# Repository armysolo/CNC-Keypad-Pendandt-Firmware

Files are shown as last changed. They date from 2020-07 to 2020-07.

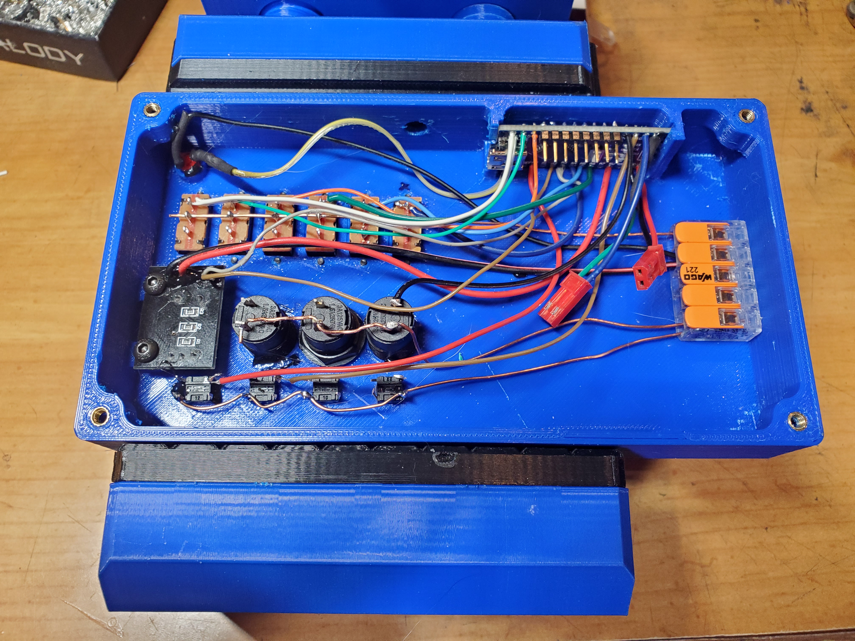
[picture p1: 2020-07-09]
Images/Assembly2.jpg

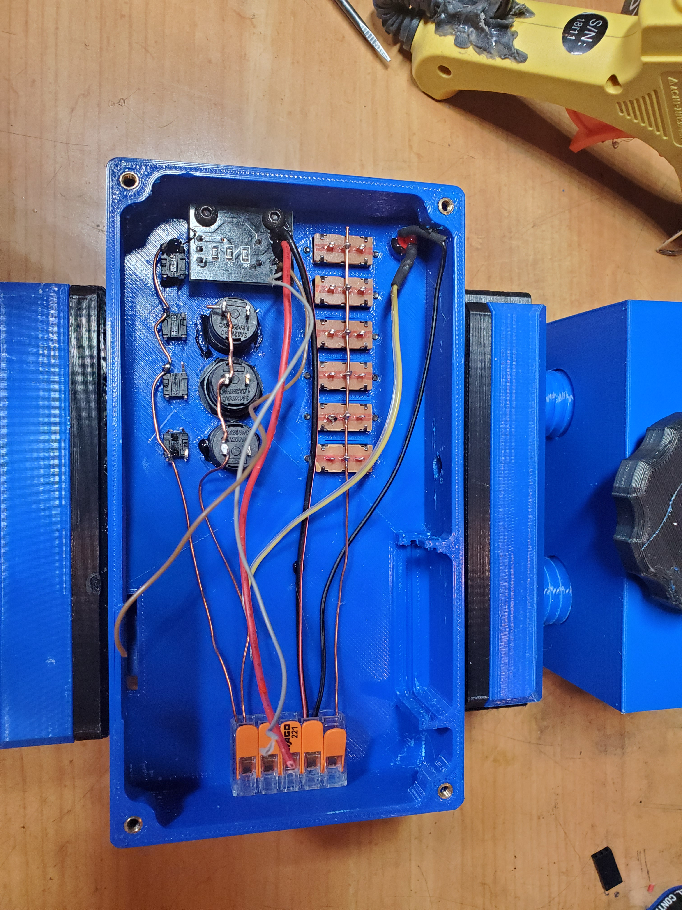
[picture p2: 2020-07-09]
Images/Assembly1.jpg

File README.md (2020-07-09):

# CNC-Pendant-Firmware

Modified CNC Pendant Firmware with Arduino Nano Clone with CH340G microchip. I didn't want to spend $80(USD) on a pendant that limited the functionality to only jogging moves. My branch keeps the functionality of jogging using a rotary encoder and common micro SPDT 1P2T switches but also incorporates a 16 button keypad where you can assign custom G/M codes or even macros. This also maintains Panel Due functionality by passing TX from the Arduino to the Duet board and RX from the Arudino to the Panel Due.

*NOTE: This should work with other Arduino boards like the Arduino Micro Pro. However my testing was done only with a Nano clone so all wiring and sketch notes are based on the Nano. There's residual info/configs from the original fork I didn't want to get rid of.

The Arduino Nano I use come un-soldered. The printed parts I designed are based off Arduino Nano clones without the pins. The parts could still work if modified but for now you'd probably have some fitment issues. You will need to solder pins to D2-D9 for the keypad. Make sure to flip the pins so the longer end of the pins are on the top instead of the bottom.

```
Nano     Connected to:   
VCC      PanelDue side port 5V
GND      PanelDue side port 0V
GND      LED - Terminal, Rotary Encoder Ground, Mini Switch Middle Terminal, Emergency Stop
5v       Rotary Encoder + Terminal, LED + Terminal-Make sure you use the correct resistor to reduce the votage from the Arduino. 120-220 ohm should be sufficient.
A0       Emergency Stop
A1       NC
A2       Rotary Encoder Pin A
A3       Rotary Encoder Pin B
A4       X Switch Top Lug
A5       Y Switch Top Lug
A6       Z Switch Top Lug
A7       NC
D2       Keypad Membrane
D3       Keypad Membrane
D4       Keypad Membrane
D5       Keypad Membrane
D6       Keypad Membrane
D7       Keypad Membrane
D8       Keypad Membrane
D9       Keypad Membrane
D10      X.1 Switch Top Lug
D11      X1 Switch Top Lug
D12      X10 Switch Top Lug
D13      NC
TX1      Through 6K8 resistor to Duet URXD0
RX0      Paneldue Dout Side Port
```

To use the jog features you will need to select your axis and the movement increments by sliding the switch up. So if you slide the X switch up and the x1 switch up, turning the rotary encoder will move the axis in 1mm increments.

Code Explanation
The G/M code you wish to assign to the keypad buttons must have a specific format. The desired G/M code goes in the quotations with "\n" at the end of each code. 

For instance 

    1. this code is assigned to button number 1 and when pressed it sends G28 to the printer. 
      if (key == '1') { output.print("G28\n"); } // Home all

You can assign a button to run multiple G/M codes at once. 

For instance 

    2. this code is assigned to button number 4. When pressed it enables the hotend and sets it's temp to 200. Notice each code must have "\n" after the end of it.
      else if (key == '4') { output.print("T0 P0\n G10 P0 S200\n"); }  // Enable hotend and set temp to 200c

This code is assigned to button number 3.

    3. When pressed it sends; M120-pushes state of the machine to a stack, M83-Sets extruder to relative position, G1-Linear move, E10 F900-Extrude 10mm of filament at 900mm per minute, M121-Recovers last state from stack
      else if (key == '3') { output.print("M120\n M83\n G1\n E10\n F900\n M121\n"); } //Extrude 10mm of filament at 15mm/s

The original sketch included a LED that would illuminate when the Estop was pressed but I found it inconsistent. The LED would often stay lit after the Estop was pressed so my sketch has the LED part removed.

I used the core from door bell wire and daisy chained all the switch grounds to clean up the wiring. 

I installed a latching push button switch where one terminal goes to ground on the Arduino and the other terminal goes to ground for all switches, rotary encoder and LED. Wiring it this way allows me to disable the rotary encoder, tactile switches and slide switches preventing any unwanted movement. When the switch is latched it enables the rotary encoder and all other switches, the LED will light up to let you know everything is grounded/enabled.

**Parts list** These are the links for reference of the parts I puchased:

**Arduino Nano Clone** These boards are so inexepensive and have so many uses I buy them 10 at a time un-soldered. With them unsoldered it's also easier to desolder the resistor on the front leading to the LED and desolder the 1k resistor on the rear and replace it with a 10k resistor. I used a little hot glue from a hot glue gun to secure the resistor to the back of the board to protect it.

**10 Pack un-soldered**
https://www.amazon.com/Longruner-ATmega328P-Controller-Module-Arduino/dp/B01MSYWE6B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

**3 Pack un-soldered**
https://www.amazon.com/WYPH-ATmega328P-Microcontroller-Development-Not-soldered/dp/B07KCH534K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

**2 Position Mini switch** If it's a 3 prong switch the middle lug is the common lug. When the switch is in the bottom position, the circuit for the bottom lug and middle lug are closed while the top lug is open. When the switch is in the top position, the circuit for the top lug and middle lug are closed while the bottom lug is open.
https://www.amazon.com/uxcell-Position-Switch-Solder-SS12F1-G3/dp/B007QAJMHO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

**Keypad membrane** 4x4 16 key keypad membrane
https://www.amazon.com/WINGONEER-Universial-Switch-Keyboard-Arduino/dp/B06XHFC19G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

**KY-040 Rotary Encoder** I desoldered the pins and soldered the wires directly to the board. The push button terminal(SW) is not connected to the Arudino.
https://www.amazon.com/Cylewet-Encoder-15%C3%9716-5-Arduino-CYT1062/dp/B06XQTHDRR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

**6 x 6mm Momentary Tactile Push Button Switch Micro NO/NC** These are 4 pin momentary push button switches. Depending which lugs you solder, the switch can be used as NO(switch circuit is open until pressed) OR NC(switch is closed until pressed). Currently used for Emergency Stop/Reset Button. Can also be used for to assign additional G/M codes.
https://www.amazon.com/gp/product/B071KX71SV/ref=ppx_yo_dt_b_search_asin_title?ie=UTF8&psc=1
**Note: Coding to support additional push button switches in prgoress.

**5mm LEDs**
https://www.amazon.com/MCIGICM-Circuit-Assorted-Science-Experiment/dp/B07PG84V17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

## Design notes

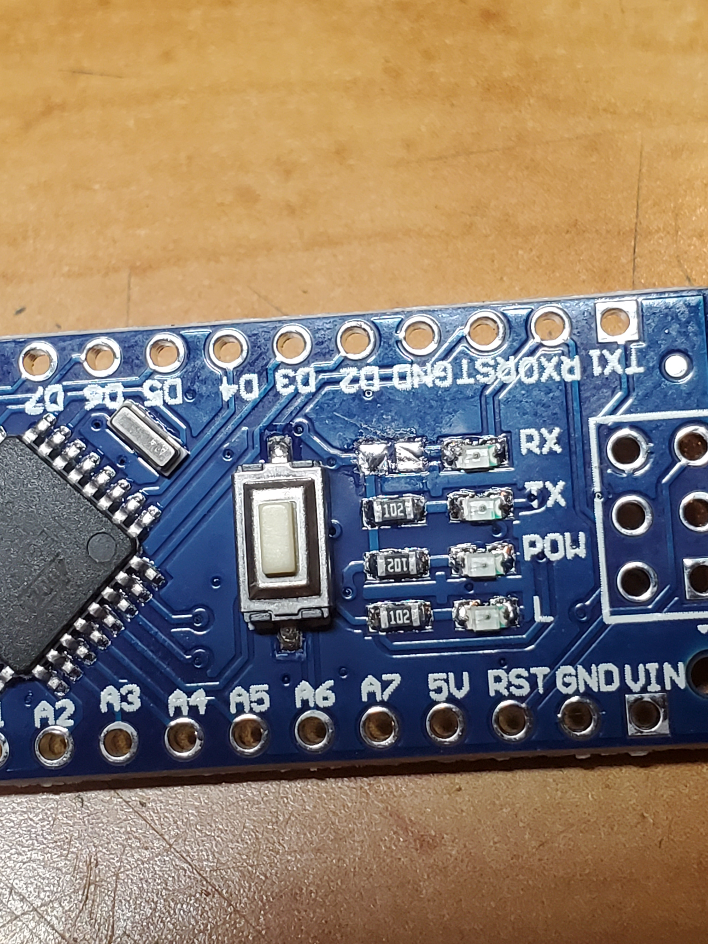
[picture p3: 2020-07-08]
Images/Nano1-2.jpg

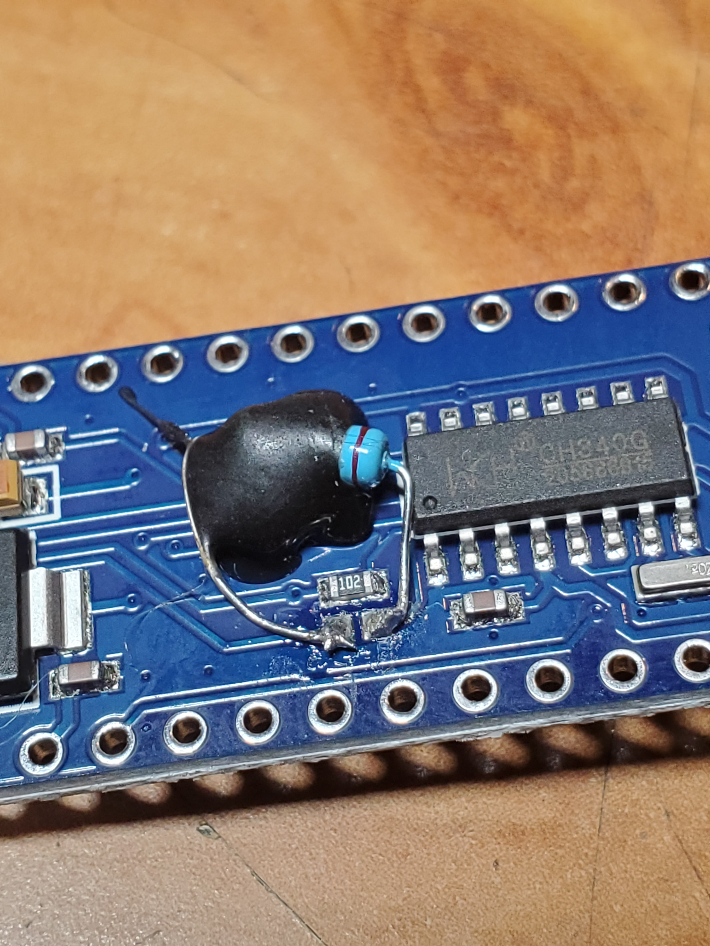
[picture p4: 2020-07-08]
Images/Nano2-2.jpg

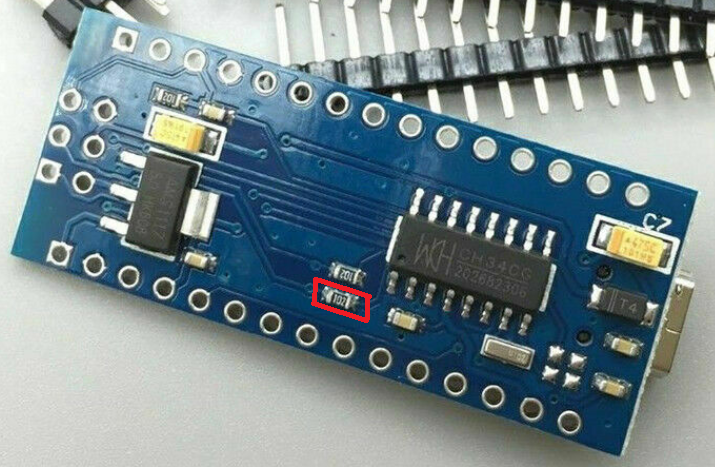
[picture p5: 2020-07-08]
Images/Nano2-1.png

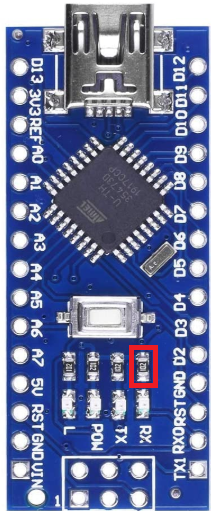
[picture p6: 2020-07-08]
Images/Nano1-1.png

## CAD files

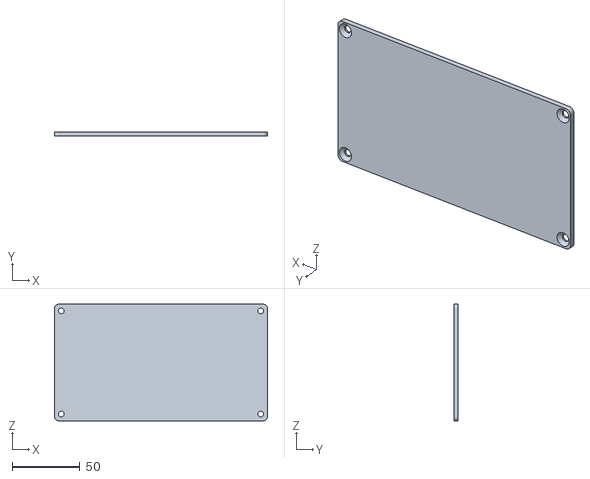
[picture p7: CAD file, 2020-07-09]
Printed Files/Mini Button Back With G Code Sender.STL
157.0 x 3.00 x 86.0

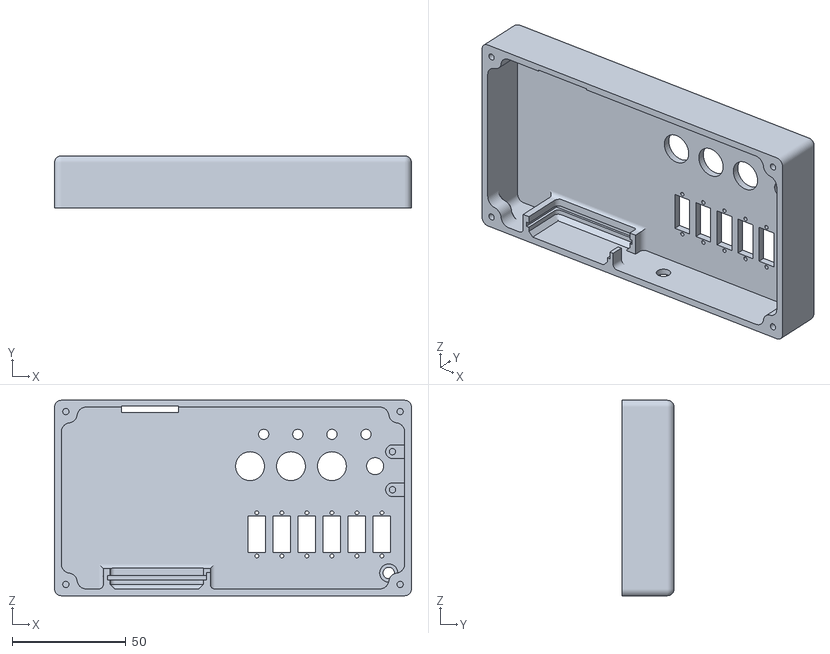
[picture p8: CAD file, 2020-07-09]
Printed Files/Mini Button Mount With G Code Sender.STL
157.0 x 23.0 x 86.0

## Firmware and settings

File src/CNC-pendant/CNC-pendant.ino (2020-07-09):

// CNC pendant interface to Duet
// D Crocker, started 2020-05-04

/* This Arduino sketch can be run on either Arduino Nano or Arduino Pro Micro. 
 * It should alo work on an Arduino Uno (using the same wiring scheme as for the Nano) or Arduino Leonardo (using the same wiring scheme as for the Pro Micro).
 * The recommended board is the Arduino Pro Micro because the passthrough works without any modificatoins to the Arduino. 

Nano     Connected to:   
VCC      PanelDue side port 5V
GND      PanelDue side port 0V
GND      LED - Terminal, Rotary Encoder Ground, Mini Switch Middle Terminal, Emergency Stop
5v       Rotary Encoder + Terminal, LED + Terminal-Make sure you use the correct resistor to reduce the votage from the Arduino. 120-220 ohm should be sufficient.
A0       Emergency Stop
A1       NC
A2       Rotary Encoder Pin A
A3       Rotary Encoder Pin B
A4       X Switch Top Lug
A5       Y Switch Top Lug
A6       Z Switch Top Lug
A7       NC
D2       Keypad Membrane
D3       Keypad Membrane
D4       Keypad Membrane
D5       Keypad Membrane
D6       Keypad Membrane
D7       Keypad Membrane
D8       Keypad Membrane
D9       Keypad Membrane
D10      X.1 Switch Top Lug
D11      X1 Switch Top Lug
D12      X10 Switch Top Lug
D13      NC
TX1      Through 6K8 resistor to Duet URXD0
RX0      Paneldue Dout Side Port

On the Arduino Nano is necessary to replace the 1K resistor between the USB interface chip by a 10K resistor so that PanelDiue can override the USB chip.
On Arduino Nano clones with CH340G chip, it is also necessary to remove the RxD LED or its series resistor.

*/

// Configuration constants
#include <Keypad.h>

const int PinA = A2;
const int PinB = A3;
const int PinX = A4;
const int PinY = A5;
const int PinZ = A6;
const int PinStop = A0;
const int PinTimes1 = 10;
const int PinTimes10 = 11;
const int PinTimes100 = 12;
const byte ROWS = 4; //four rows
const byte COLS = 4; //four columns
//Installed Upright/Normal
char hexaKeys[ROWS][COLS] = {
       {'1','2','3','A'},
       {'4','5','6','B'},
       {'7','8','9','C'},
       {'*','0','#','D'}
    };

byte rowPins[ROWS] = {2, 3, 4, 5};
byte colPins[COLS] = {6, 7, 8, 9};


Keypad keypad = Keypad( makeKeymap(hexaKeys), rowPins, colPins, ROWS, COLS);

const unsigned long BaudRate = 57600;
const int PulsesPerClick = 4;
const unsigned long MinCommandInterval = 20;

// Table of commands we send, one entry for each axis
const char* const MoveCommands[] =
{
  "G91 G0 F6000 X",     // X axis
  "G91 G0 F6000 Y",     // Y axis
  "G91 G0 F600 Z",      // Z axis
};

#include "RotaryEncoder.h"
#include "GCodeSerial.h"
#include "PassThrough.h"

RotaryEncoder encoder(PinA, PinB, PulsesPerClick);
PassThrough passThrough;

int serialBufferSize;
int distanceMultiplier;
int axis;
uint32_t whenLastCommandSent = 0;

const int axisPins[] = { PinX, PinY, PinZ, };
const int feedAmountPins[] = { PinTimes1, PinTimes10, PinTimes100 };

# define UartSerial   Serial

GCodeSerial output(UartSerial);

void setup()
{
  pinMode(PinA, INPUT_PULLUP);
  pinMode(PinB, INPUT_PULLUP);
  pinMode(PinX, INPUT_PULLUP);
  pinMode(PinY, INPUT_PULLUP);
  pinMode(PinZ, INPUT_PULLUP);
  pinMode(PinTimes1, INPUT_PULLUP);
  pinMode(PinTimes10, INPUT_PULLUP);
  pinMode(PinTimes100, INPUT_PULLUP);
  pinMode(PinStop, INPUT_PULLUP);
  output.begin(BaudRate);
  serialBufferSize = output.availableForWrite();
  Serial.begin(57600);
  keypad.addEventListener(keypadEvent);  //Keypad 1
}

// Check for received data from PanelDue, store it in the pass through buffer, and send it if we have a complete command
void checkPassThrough()
{
  unsigned int commandLength = passThrough.Check(UartSerial);
  if (commandLength != 0 && UartSerial.availableForWrite() == serialBufferSize)
  {
    output.write(passThrough.GetCommand(), commandLength);
  }
}

void loop()
{
  // 0. Poll the encoder. Ideally we would do this in the tick ISR, but after all these years the Arduino core STILL doesn't let us hook it.
  // We could possibly use interrupts instead, but if the encoder suffers from contact bounce then that isn't a good idea.
  // In practice this loop executes fast enough that polling it here works well enough
  encoder.poll();

  // 1. Check for emergency stop
  if (digitalRead(PinStop) == LOW)
  {
    // Send emergency stop command every 2 seconds
    do
    {
      output.write("M112 ;" "\xF0" "\x0F" "\n");
      uint16_t now = (uint16_t)millis();
      while (digitalRead(PinStop) == HIGH && (uint16_t)millis() - now < 2000)
      {
        checkPassThrough();
      }
      encoder.getChange();      // ignore any movement
    } while (digitalRead(PinStop) == HIGH);

    output.write("M999\n");
  }
  char key = keypad.getKey();  //Keypad 1

  // 2. Poll the feed amount switch
  distanceMultiplier = 0;
  int localDistanceMultiplier = 1;
  for (int pin : feedAmountPins)
  {
    if (digitalRead(pin) == LOW)
    {
      distanceMultiplier = localDistanceMultiplier;
      break;
    }
    localDistanceMultiplier *= 10;
  }

  // 3. Poll the axis selector switch
  axis = -1;
  int localAxis = 0;
  for (int pin : axisPins)
  {
    if (digitalRead(pin) == LOW)
    {
      axis = localAxis;
      break;
    }
    ++localAxis;    
  }
  
  // 5. If the serial output buffer is empty, send a G0 command for the accumulated encoder motion.
  if (output.availableForWrite() == serialBufferSize)
  {
    const uint32_t now = millis();
    if (now - whenLastCommandSent >= MinCommandInterval)
    {
      int distance = encoder.getChange() * distanceMultiplier;
      if (axis >= 0 && distance != 0)
      {
        whenLastCommandSent = now;
        output.write(MoveCommands[axis]);
        if (distance < 0)
        {
          output.write('-');
          distance = -distance;
        }
        output.print(distance/10);
        output.write('.');
        output.print(distance % 10);
        output.write('\n');
      }
    }
  }

  checkPassThrough();
}

void keypadEvent(KeypadEvent key) {
  switch (keypad.getState()) {
    
    /* About getState: the PRESSED state occurs first, right when the users presses a key.
     * Following PRESSED the next state can be either HOLD or RELEASED.
     * If the key is pressed longer than 500 milliseconds (default) you will reach the HOLD state.  
     * However, if the key was pressed and released in less than 500 milliseconds then the next state is RELEASED.
     * The RELEASED state occurs after a PRESSED or HOLD state and only after the user lets go of the key.
    */
    
    case PRESSED:

        //row1
             if (key == '1') { output.print("G28\n"); } // Home all 
        else if (key == '2') { output.print("G32\n"); } // Bed Leveling
        else if (key == '3') { output.print("M120\n M83\n G1\n E10\n F900\n M121\n"); } //Extrude 10mm of filament at 15mm/s
        else if (key == 'A') { output.print("M120\n M83\n G1\n E-10\n F900\n M121\n"); } //Extrude 10mm of filament at 15mm/s
        //row2
        else if (key == '4') { output.print("T0 P0\n G10 P0 S200\n"); }  // Enable hotend and set temp to 200c
        else if (key == '5') { output.print("T-1 P0\n G10 P0S-273.15 R-273.15\n"); }  // Turn hotend off
        else if (key == '6') { output.print("M140 S60\n"); }  // Heatbed to 60c
        else if (key == 'B') { output.print("M140 S0\n M140 S-273.15\n"); } // Turn heatbed off
        //row3
        else if (key == '7') { output.print("M106 S0.90\n"); } // Turn fan on to 90%
        else if (key == '8') { output.print("M106 S0\n"); } // Turn fan on off
        else if (key == '9') { output.print("M112\n"); } // Emergency Stop
        else if (key == 'C') { output.print("M112+M999\n"); } // Emergency stop and reset board
        //row4
        else if (key == '*') { output.print("M558 P9\n G31 P500 Z1.0\n"); } // Set Z Probe to BLTouch and probe the bed at current position
        else if (key == '0') { output.print("G92 Z10\n"); } // Set Current Z Height to 10
        else if (key == '#') { output.print("G92 Z0\n"); } // Set Current Z Height to 0
        else if (key == 'D') { output.print("G30 S-1\n"); } // Probe the bed at the current position
        break;

    case RELEASED:        
        break;

    case HOLD:
        break;
  }
}
// End
